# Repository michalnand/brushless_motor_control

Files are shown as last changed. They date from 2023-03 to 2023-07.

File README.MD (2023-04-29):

# stm32 FOC brushless motor controller

board

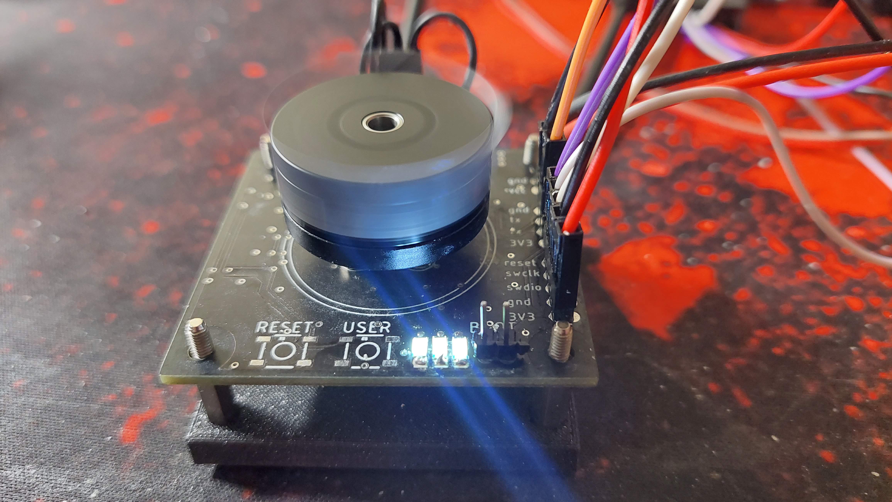
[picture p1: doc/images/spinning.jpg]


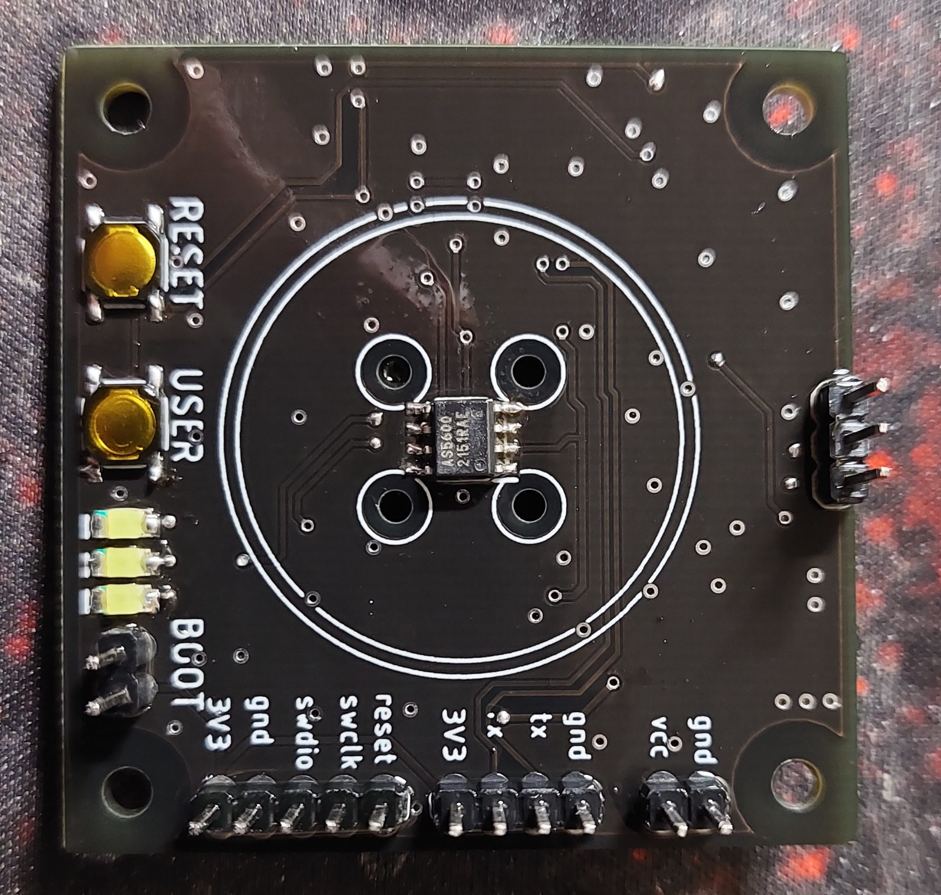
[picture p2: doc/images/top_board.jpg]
board

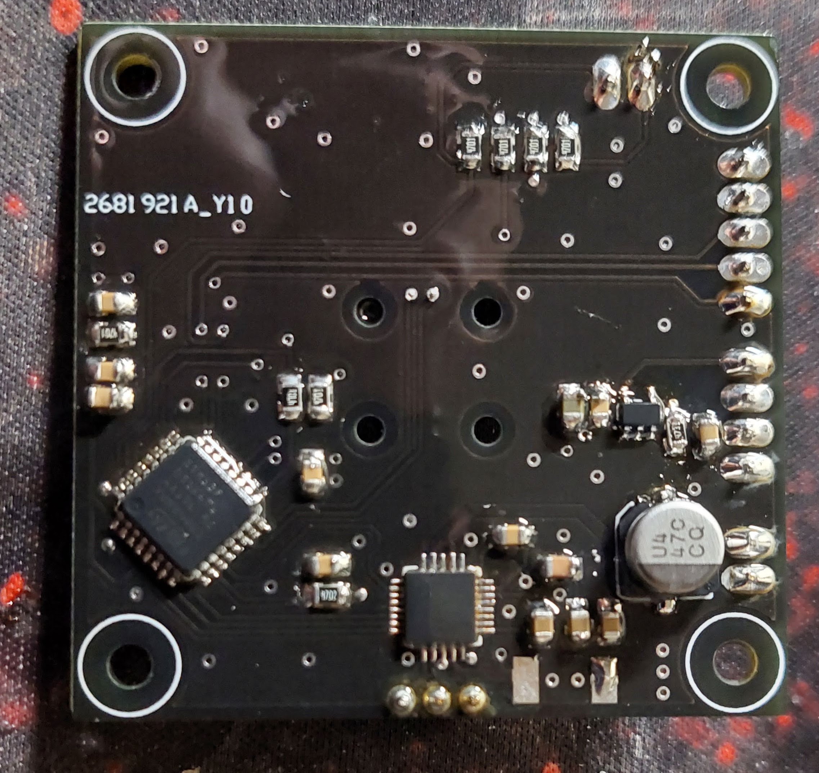
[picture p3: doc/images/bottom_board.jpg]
board


# repository

## utils : [utils](utils)
- testing utils and simulations
- transformation tests : transform_test.py
- PI current synthetis : pi_torque.ipynb
- LQR synthetis : lqr_design.ipynb
- requires [LibsControll](https://github.com/michalnand/libs_control)

## hardware : [hardware](hardware)
- eagle files
- 3D priting parts (jig for magnet centering)
- IMPORTANT - in schematic is wrong MP6540HA, correct is MP6540H (pwm only driver with enable)

- MCU   : stm32f051, arm cortex m0, 48MHz
- 3phase driver : MP6540H (DONT MP6540HA), 5A, 50V
- encoder : AS5600, 12bit, i2c

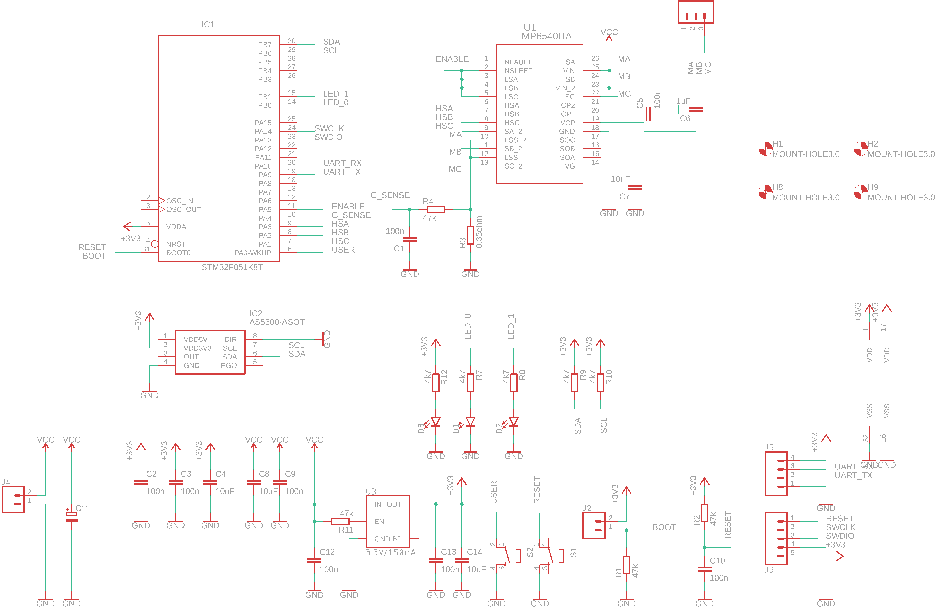
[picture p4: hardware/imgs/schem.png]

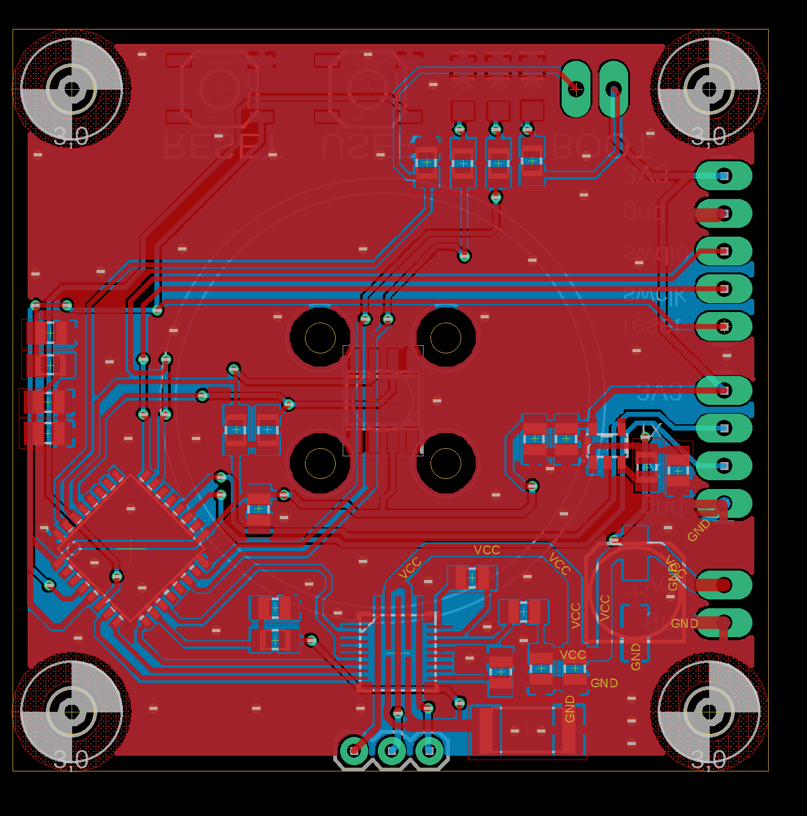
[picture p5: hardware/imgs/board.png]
board


## firmware : [firmware](firmware)
- main code for stm32f051
- core is in **user** folder
- see motor.cpp and motor_control.cpp to understand all details

# FOC block diagrams

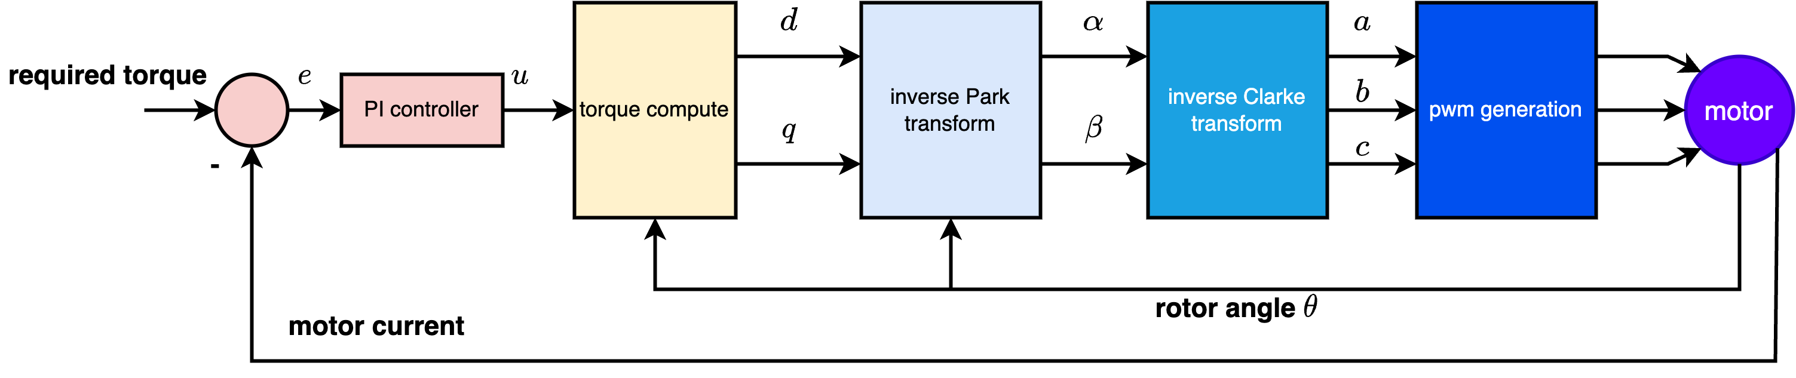
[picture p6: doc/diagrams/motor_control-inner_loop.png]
inner_loop


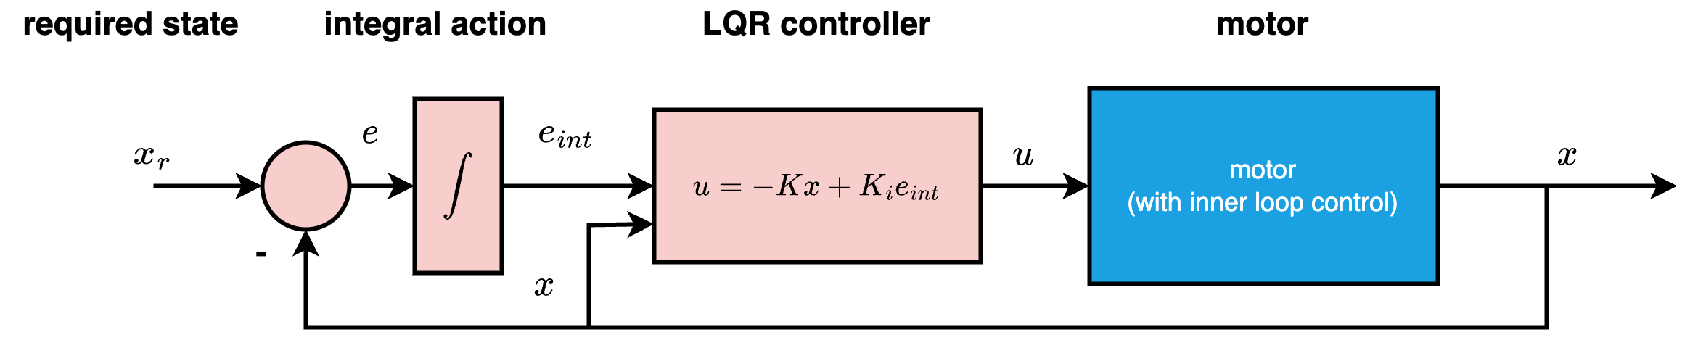
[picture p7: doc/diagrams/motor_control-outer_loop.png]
outer_loop


# transformation tests

basic tranformations tests :
- clarke - park - pwm scaling
- see [transform_test.py](utils/transform_test.py)

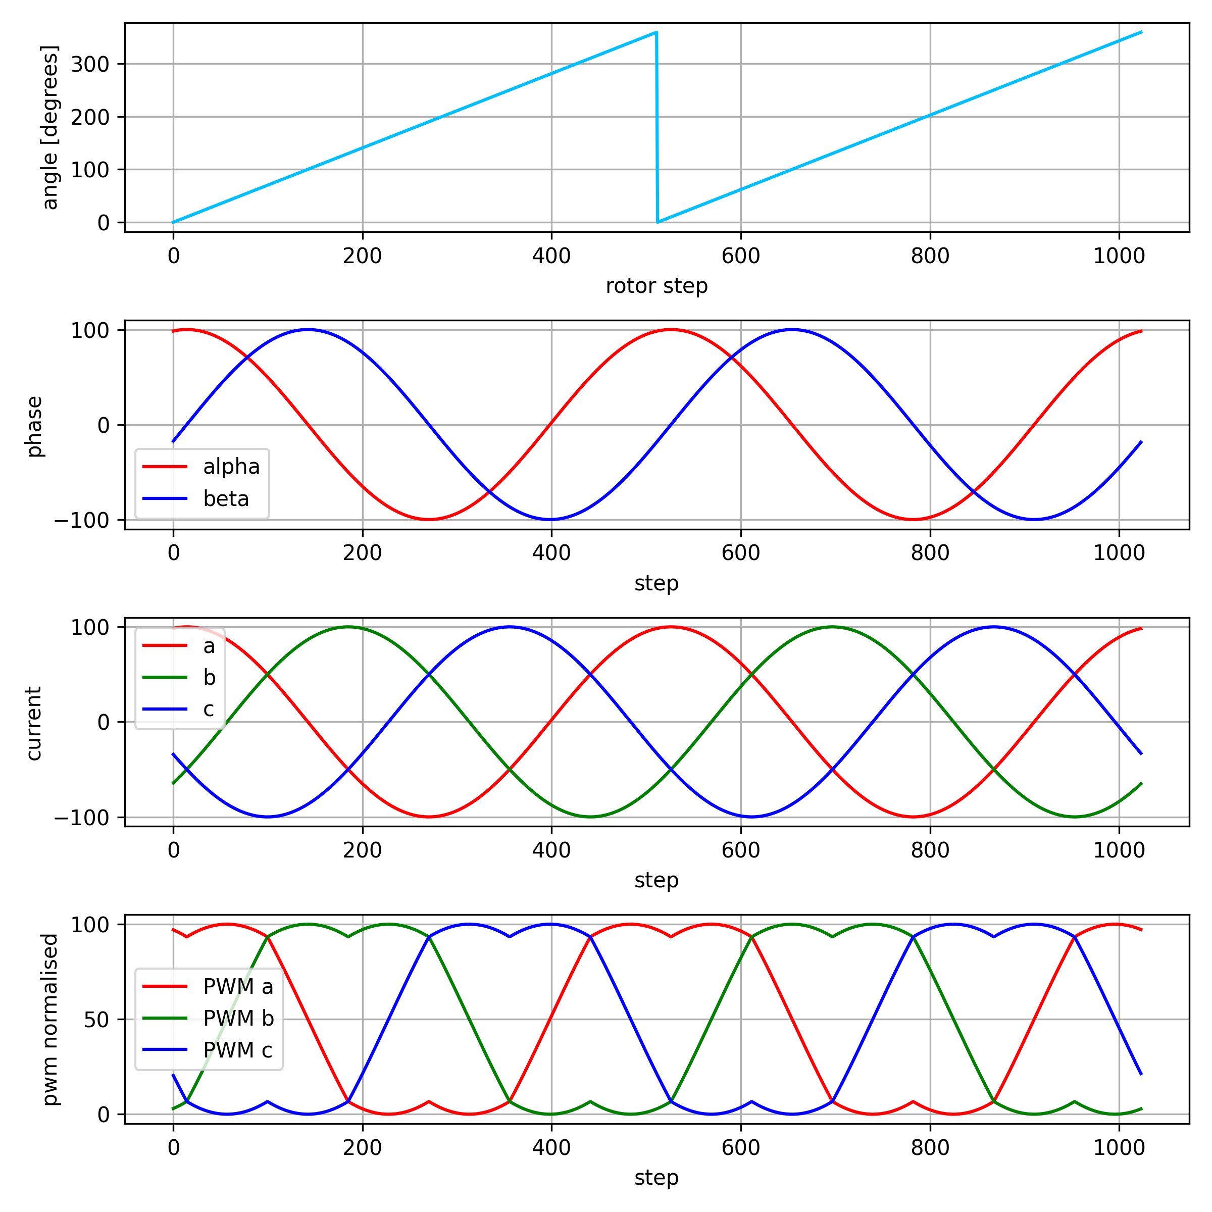
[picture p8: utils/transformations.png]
transformations


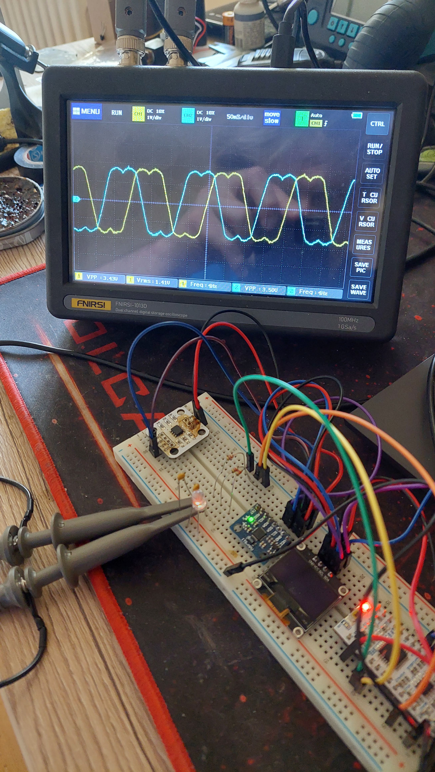
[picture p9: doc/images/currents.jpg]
currents


# fast running transformations in fixed point

## key features

- sine and cosine is precomputed, 1024 values arrays
- angle 2pi == 1024 (or 0) into tables
- theta ranges from <0, 1023>
- SINE_TABLE_MAX  represents "one", 1023 in tables
- square root of 3 is also precomputed, as fraction of x/1024 
- all divisions are by power of 2 - to avoid slow division
- this can easily run few kHz on cortex m0 (48MHz ARM)

```c++

#define SQRT3       ((int32_t)1773)      // sqrt(3)     = 1773/1024
#define SQRT3INV    ((int32_t)591)       // 1/sqrt(3)   = 591/1024

void Motor::set_park(int32_t d, int32_t q, uint32_t theta)
{
    //inverse Park transform
    int32_t alpha = (d*cos_tab(theta) - q*sin_tab(theta))/SINE_TABLE_MAX;
    int32_t beta  = (d*sin_tab(theta) + q*cos_tab(theta))/SINE_TABLE_MAX;

    this->set_clarke(alpha, beta);
}

void Motor::set_clarke(int32_t alpha, int32_t beta)
{
    //inverse Clarke transform
    int32_t a = alpha;
    int32_t b = -(alpha/2) + (SQRT3*beta)/(2*1024);
    int32_t c = -(alpha/2) - (SQRT3*beta)/(2*1024);

    this->set_phases(a, b, c); 
}

void Motor::set_phases(int32_t a, int32_t b, int32_t c)
{
    //transform into space-vector modulation, to achieve full voltage range
    int32_t min_val = min3(a, b, c);
    int32_t max_val = max3(a, b, c); 

    int32_t com_val = (min_val + max_val)/2;  

    //normalise into 0..MOTOR_CONTROL_MAX
    int32_t a_pwm = ((a - com_val)*SQRT3INV)/1024 + MOTOR_CONTROL_MAX/2;
    int32_t b_pwm = ((b - com_val)*SQRT3INV)/1024 + MOTOR_CONTROL_MAX/2;
    int32_t c_pwm = ((c - com_val)*SQRT3INV)/1024 + MOTOR_CONTROL_MAX/2;

    a_pwm = clamp((a_pwm*PWM_PERIOD)/MOTOR_CONTROL_MAX, 0, PWM_PERIOD);
    b_pwm = clamp((b_pwm*PWM_PERIOD)/MOTOR_CONTROL_MAX, 0, PWM_PERIOD);
    c_pwm = clamp((c_pwm*PWM_PERIOD)/MOTOR_CONTROL_MAX, 0, PWM_PERIOD);

    set_pwm(a_pwm, b_pwm, c_pwm);
}
```

# fast running PID in fixed point

- controller is first discretised in constructor 
- dt is sampling period in miliseconds
- kp, ki, kd are common controller constants, multiplied by 16384, to avoid floating point

```c++
k0 = kp + ((ki*dt)/1000) + ((kd*1000)/dt);
k1 = -kp - 2*((kd*1000)/dt);
k2 = ((kd*1000)/dt); 
```

- whole PID is just 3 multiplications and 4 additions
- to avoid integral windup, only clamping output is necessary 

```c++
int32_t PID::step(int32_t error)
{
    this->e2 = this->e1;
    this->e1 = this->e0;
    this->e0 = error;

    int32_t du = (k0*e0 + k1*e1 + k2*e2)/16384;
    u+= du;

    //anti windup
    if (u > antiwindup_max)
    {
        u = antiwindup_max;
    }
    
    if (u < antiwindup_min)
    {
        u = antiwindup_min;
    }

    return u;
}
```

# LQR position controller

see [lqr_design.ipynb](utils/lqr_design.ipynb)

## whole controller structure

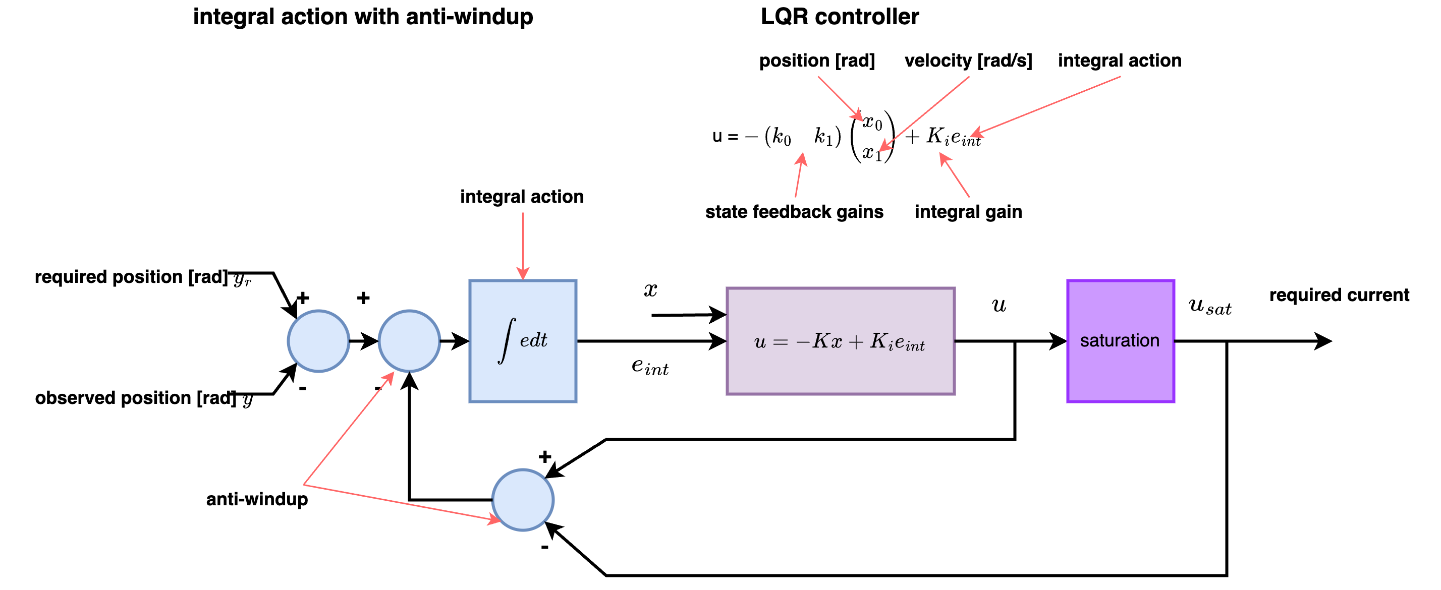
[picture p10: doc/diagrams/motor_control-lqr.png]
lqr_structure


## closed loop response + disturbance rejection

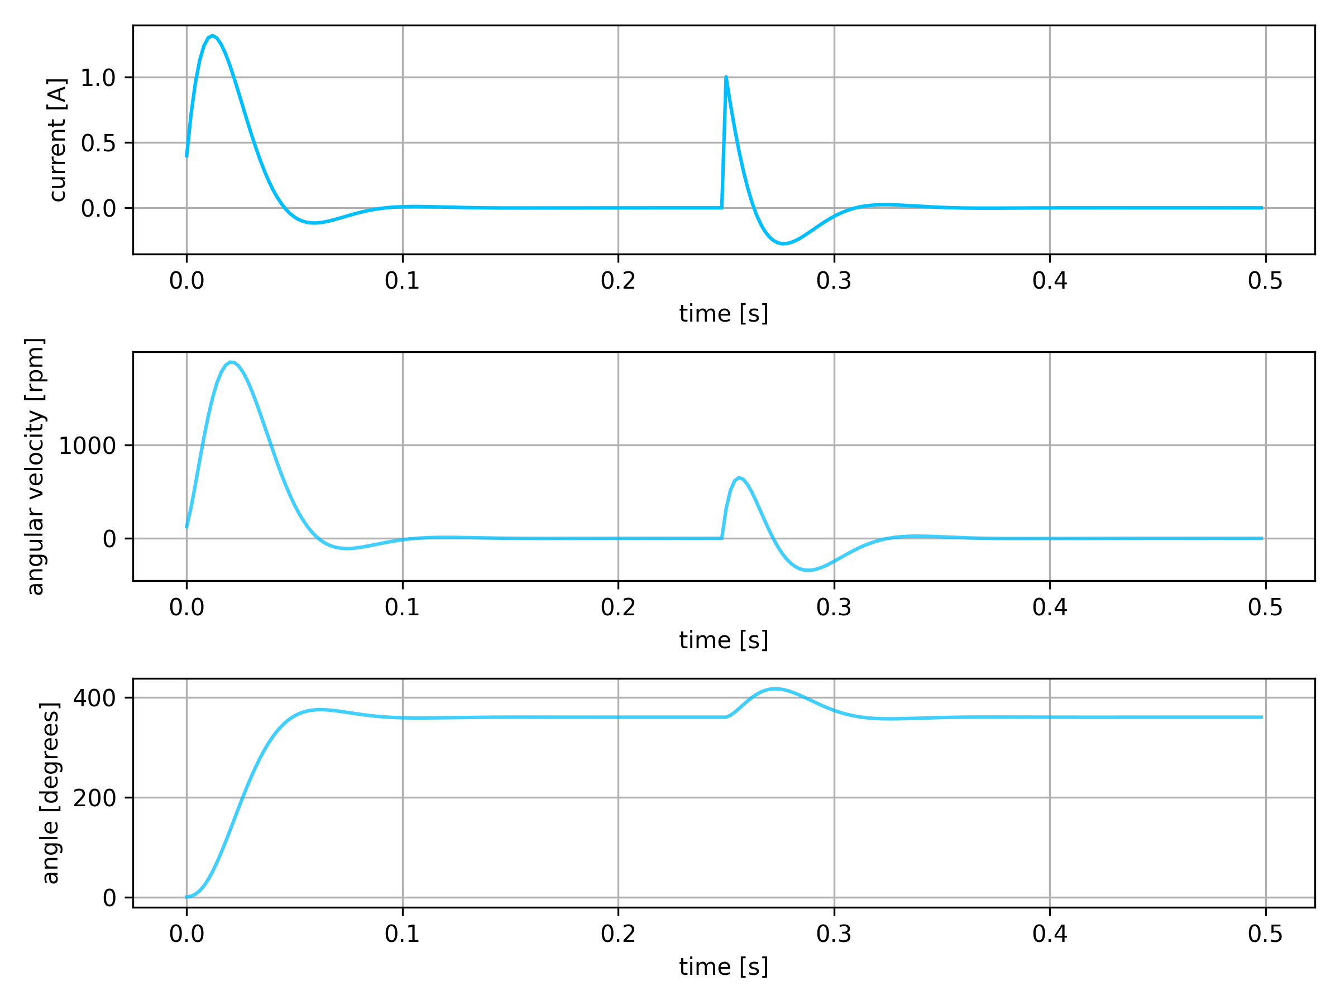
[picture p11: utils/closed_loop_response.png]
closed_loop_response


## poles

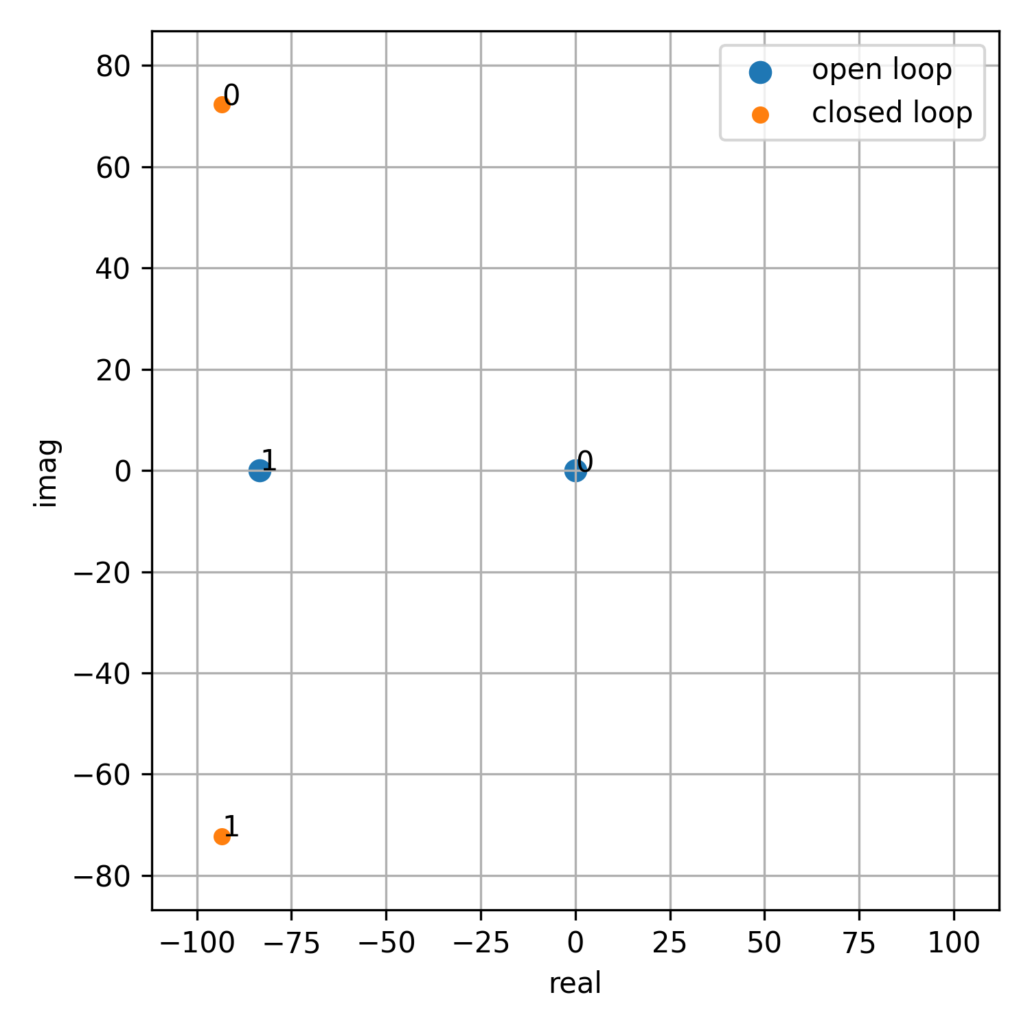
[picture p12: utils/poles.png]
poles


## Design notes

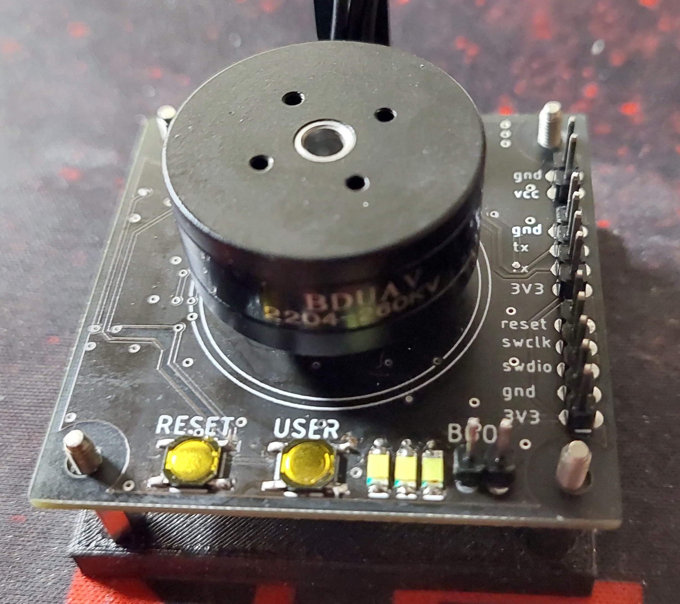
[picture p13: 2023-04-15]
doc/images/side_baord.jpg

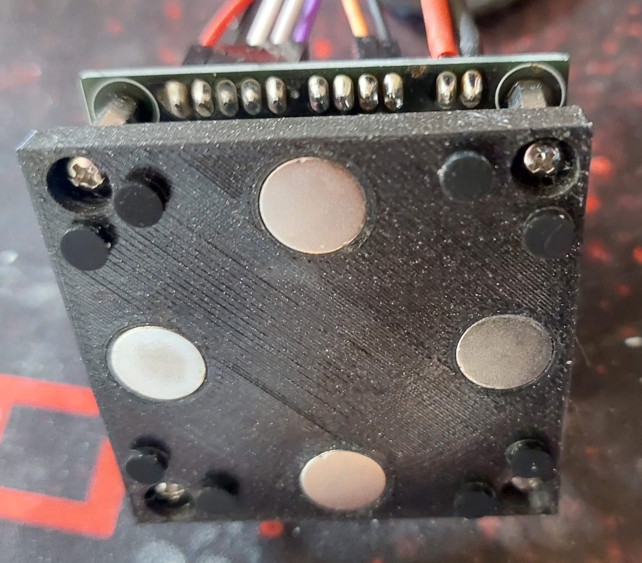
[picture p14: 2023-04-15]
doc/images/magnets.jpg

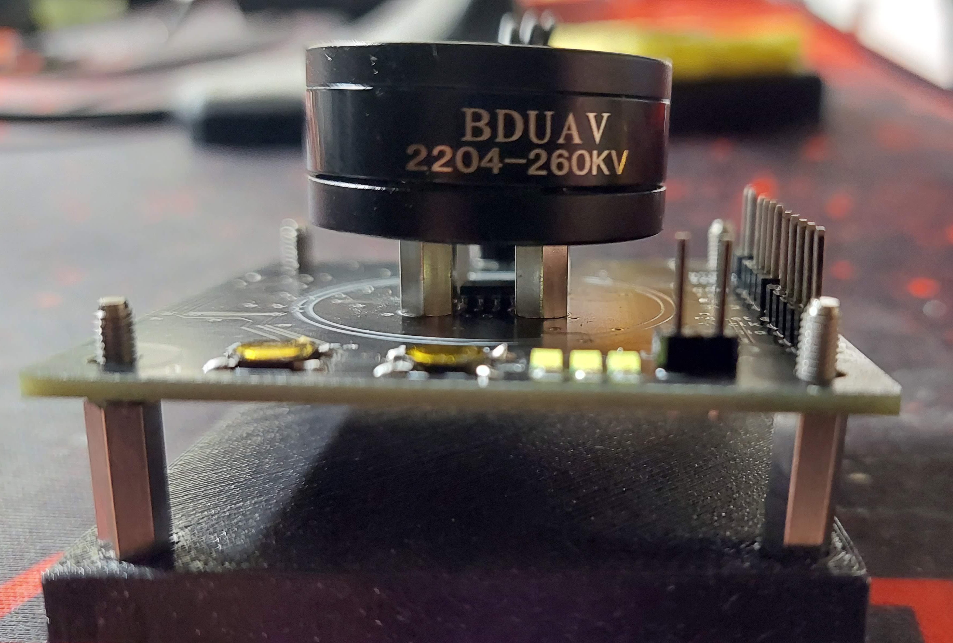
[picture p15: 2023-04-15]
doc/images/side_2_board.jpg

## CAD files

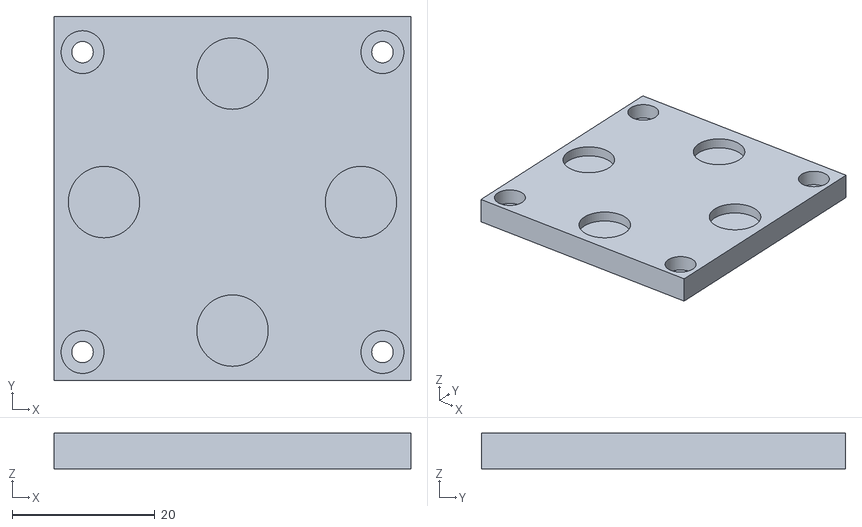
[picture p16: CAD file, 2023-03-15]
hardware/3d_print/motor_board_stand.stl
50.0 x 51.0 x 5.00

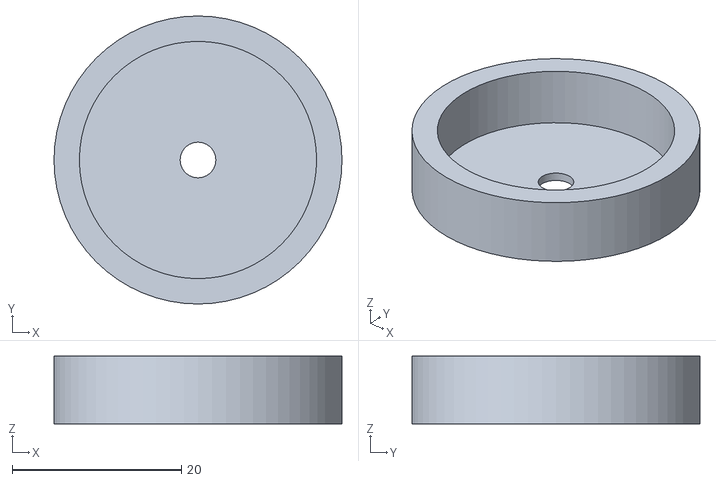
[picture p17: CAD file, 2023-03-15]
hardware/3d_print/magnet_center_jig.stl
34.0 x 34.0 x 8.00

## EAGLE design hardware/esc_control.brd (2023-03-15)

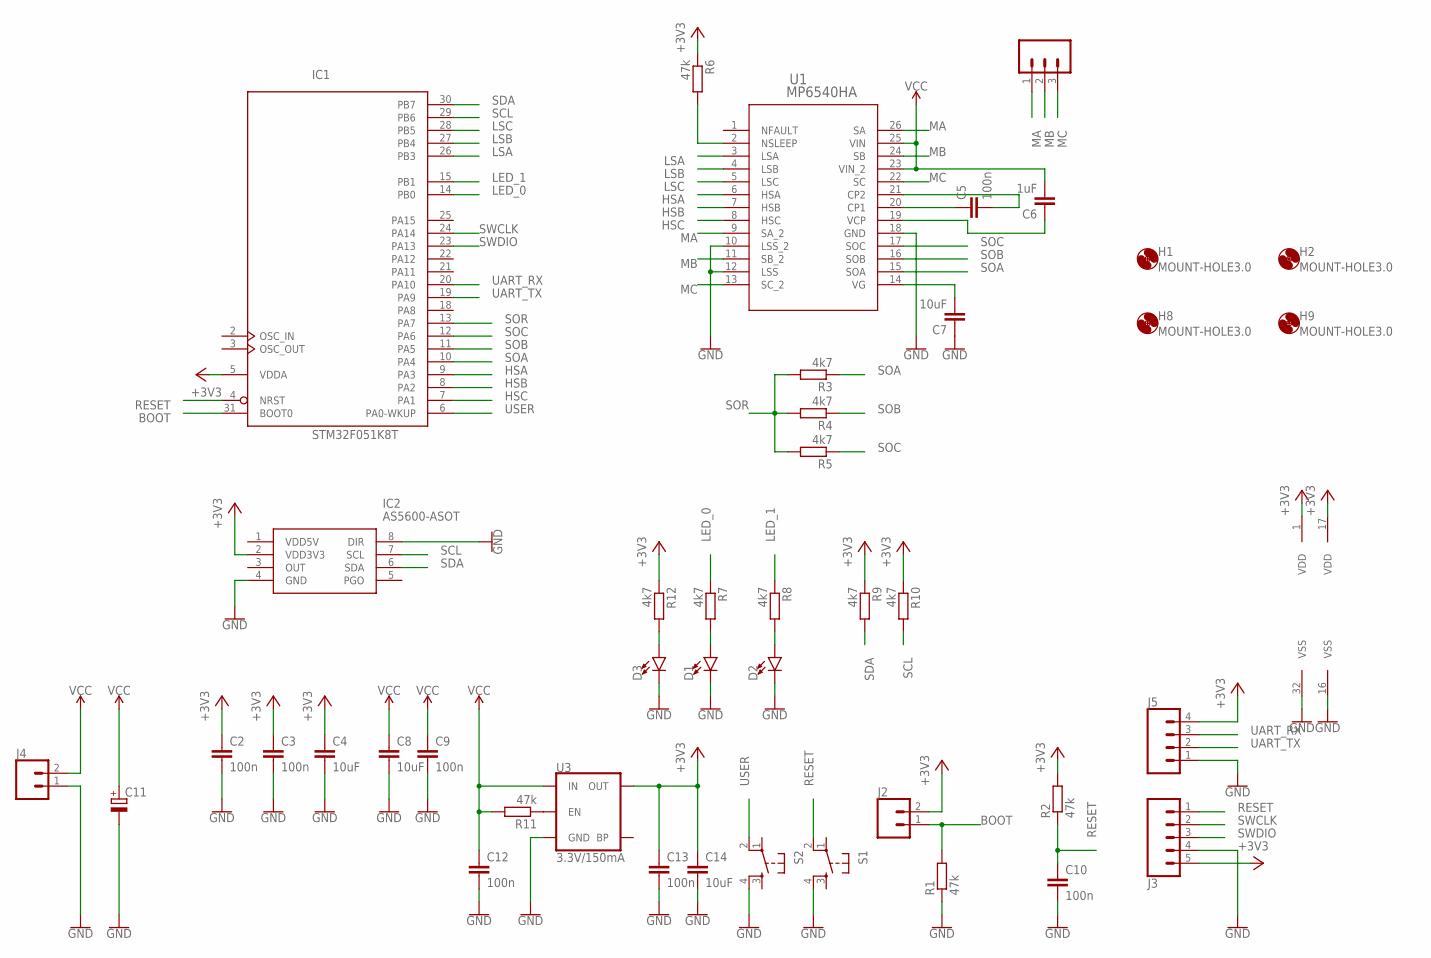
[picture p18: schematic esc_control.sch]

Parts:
C2, C3, C5, C9, C10, C12, C13: 100n; C0805
C4, C7, C8, C14: 10uF; C0805
C6: 1uF; C0805
C11: CPOL-EU153CLV-0605; 153CLV-0605
D1, D2, D3: LED1206; LED-1206
H1, H2, H8, H9: MOUNT-HOLE3.0; 3,0
IC1: STM32F051K8T; LQFP32
IC2: AS5600-ASOT; SOIC127P600X175-8N
J1: 455-1750-1-ND; 1X03
J2, J4: CONN_02PTH3; 1X02_LONGPADS
J3: CONN_05PTH_LONGPADS; 1X05_LONGPADS
J5: CONN_04LONGPADS; 1X04_LONGPADS
R1, R2, R6, R11: 47k; M0805
R3, R4, R5, R7, R8, R9, R10, R12: 4k7; M0805
S1, S2: TAC_SWITCHSMD; TACTILE-SWITCH-SMD
U1: MP6540HA; QFN-5X5_MP6540HA_MNP
U3: 3.3V/150mA; SOT23-5

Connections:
+3V3: C2.1, C3.1, C4.1, C13.1, C14.1, IC1.1 (VDD), IC1.5 (VDDA), IC1.17 (VDD), IC2.2 (VDD3V3), J2.2, J3.5, J5.4, R2.2, R6.1, R9.1, R10.1, R12.1, U3.5 (OUT)
BOOT: IC1.31 (BOOT0), J2.1, R1.2
GND: C2.2, C3.2, C4.2, C7.1, C8.2, C9.2, C10.2, C11.-, C12.2, C13.2, C14.2, D1.C, D2.C, D3.C, IC1.16 (VSS), IC1.32 (VSS), IC2.4 (GND), IC2.8 (DIR), J3.4, J4.1, J5.1, R1.1, S1.4, S2.4, U1.10 (LSS_2), U1.12 (LSS), U1.18 (GND), U3.2 (GND)
HSA: IC1.9 (PA3), U1.6 (HSA)
HSB: IC1.8 (PA2), U1.7 (HSB)
HSC: IC1.7 (PA1), U1.8 (HSC)
LED_0: IC1.14 (PB0), R7.1
LED_1: IC1.15 (PB1), R8.1
LSA: IC1.26 (PB3), U1.3 (LSA)
LSB: IC1.27 (PB4), U1.4 (LSB)
LSC: IC1.28 (PB5), U1.5 (LSC)
MA: J1.1, U1.9 (SA_2), U1.26 (SA)
MB: J1.2, U1.11 (SB_2), U1.24 (SB)
MC: J1.3, U1.13 (SC_2), U1.22 (SC)
unnamed: C5.1, U1.20 (CP1)
unnamed: C5.2, U1.21 (CP2)
unnamed: C6.1, U1.19 (VCP)
unnamed: R6.2, U1.2 (NSLEEP)
unnamed: C7.2, U1.14 (VG)
unnamed: D1.A, R7.2
unnamed: D2.A, R8.2
unnamed: R11.1, U3.3 (EN)
unnamed: D3.A, R12.2
RESET: C10.1, IC1.4 (NRST), J3.1, R2.1, S1.2
SCL: IC1.29 (PB6), IC2.7 (SCL), R10.2
SDA: IC1.30 (PB7), IC2.6 (SDA), R9.2
SOA: IC1.10 (PA4), R3.1, U1.15 (SOA)
SOB: IC1.11 (PA5), R4.1, U1.16 (SOB)
SOC: IC1.12 (PA6), R5.1, U1.17 (SOC)
SOR: IC1.13 (PA7), R3.2, R4.2, R5.2
SWCLK: IC1.24 (PA14), J3.2
SWDIO: IC1.23 (PA13), J3.3
UART_RX: IC1.20 (PA10), J5.3
UART_TX: IC1.19 (PA9), J5.2
USER: IC1.6 (PA0-WKUP), S2.2
VCC: C6.2, C8.1, C9.1, C11.+, C12.1, J4.2, R11.2, U1.23 (VIN_2), U1.25 (VIN), U3.1 (IN)

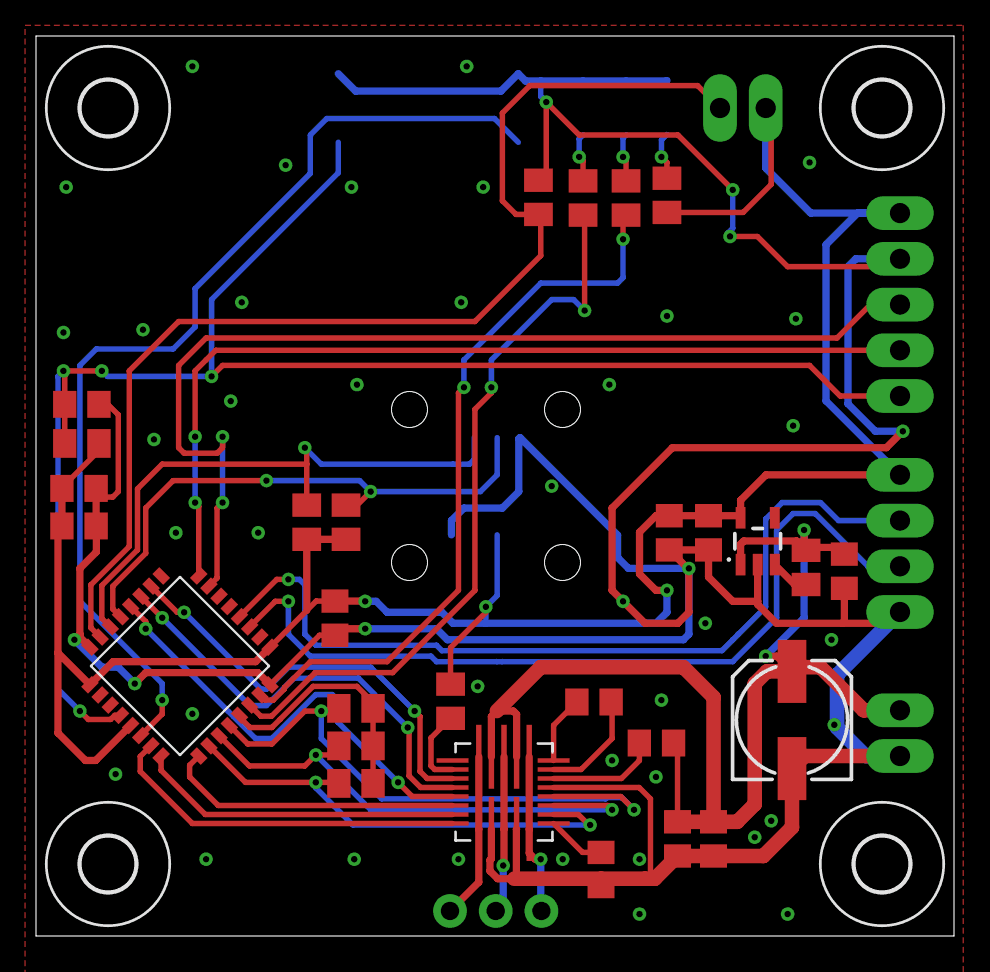
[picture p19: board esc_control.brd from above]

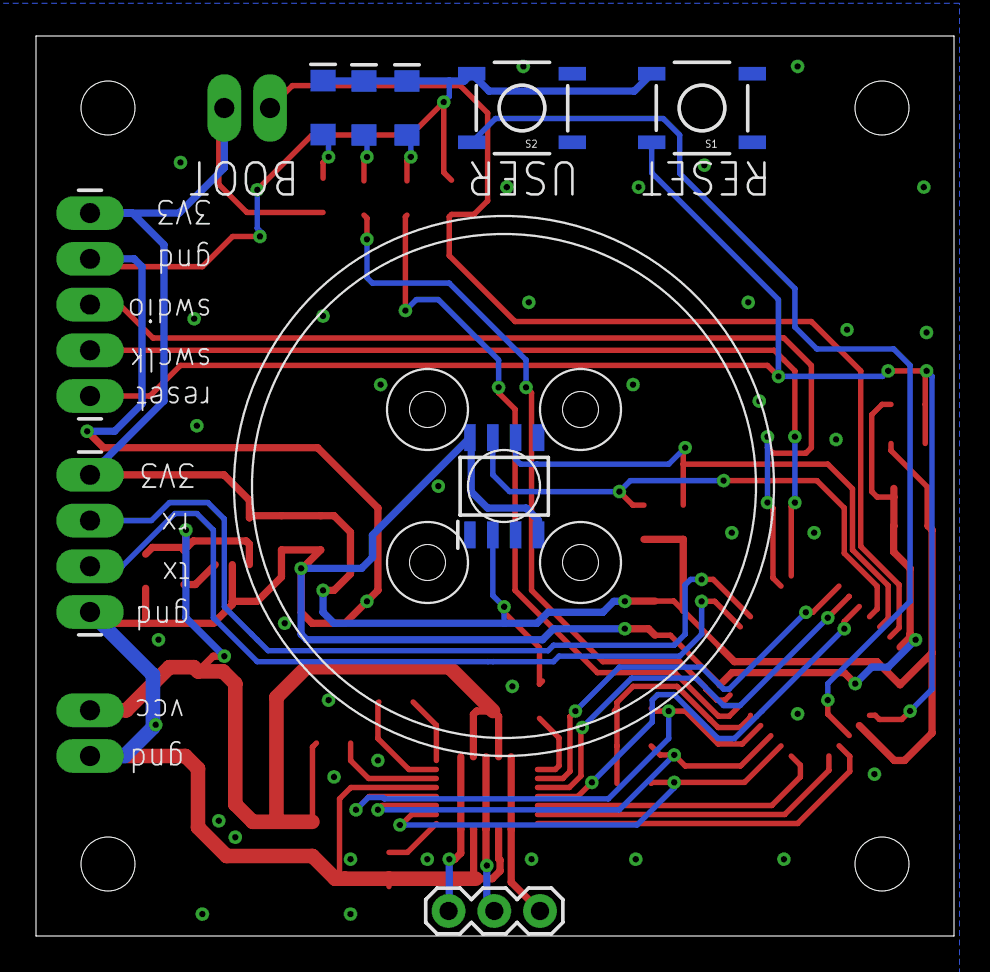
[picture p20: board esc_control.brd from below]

Board: 2 copper layers, 51.0 x 50.0 mm, 44 parts (12 on the bottom side), 36 nets.

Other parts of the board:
U$1: BRUSHLESS_GIMBAL_MOTOR_2204

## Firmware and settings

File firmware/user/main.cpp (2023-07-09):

#include "device.h"
#include <gpio.h>

#include <adc.h>
#include <i2c.h>
#include <as5600.h>
#include <motor.h>
#include <motor_control.h>

#include <gonio.h>

#include <test.h>
#include <terminal.h>
 
void SetPLL()
{
  RCC_PLLConfig(RCC_PLLSource_HSI, RCC_PLLMul_12);
  RCC_PLLCmd(ENABLE); 

  // Wait for PLLRDY after enabling PLL.
  while (RCC_GetFlagStatus(RCC_FLAG_PLLRDY) != SET)
  { 
    __asm("nop");
  } 

  // Select the PLL as clock source.
  RCC_SYSCLKConfig(RCC_SYSCLKSource_PLLCLK);  
  SystemCoreClockUpdate();
}


void delay_loops(uint32_t loops)
{
  while (loops--)
  {
    __asm("nop");
  }
}



MotorControl *g_motor_control;
volatile uint32_t g_ms_time = 0;

#ifdef __cplusplus
extern "C" {
#endif

void TIM16_IRQHandler(void)
{ 
  g_motor_control->callback_torque();
  g_ms_time++;
  TIM_ClearITPendingBit(TIM16, TIM_IT_CC1);  
}
 
void TIM17_IRQHandler(void)
{
    g_motor_control->callback(); 

    TIM_ClearITPendingBit(TIM17, TIM_IT_CC1);  
}
 
#ifdef __cplusplus
}
#endif
 
 
void timers_init()
{  
    TIM_TimeBaseInitTypeDef     TIM_TimeBaseStructure;
    NVIC_InitTypeDef            NVIC_InitStructure;

    //set timer 16 for 1kHz, and highest priority
    RCC_APB2PeriphClockCmd(RCC_APB2Periph_TIM16, ENABLE);

    TIM_TimeBaseStructure.TIM_Prescaler         = 0;
    TIM_TimeBaseStructure.TIM_CounterMode       = TIM_CounterMode_Up;
    TIM_TimeBaseStructure.TIM_Period            = 24000 - 1; //1kHz, 24MHz clock / 1000 - 1
    TIM_TimeBaseStructure.TIM_ClockDivision     = 0; 
    TIM_TimeBaseStructure.TIM_RepetitionCounter = 0;   

    TIM_TimeBaseInit(TIM16, &TIM_TimeBaseStructure);
    TIM_ITConfig(TIM16, TIM_IT_CC1, ENABLE);
    TIM_Cmd(TIM16, ENABLE); 

    NVIC_InitStructure.NVIC_IRQChannel = TIM16_IRQn;
    NVIC_InitStructure.NVIC_IRQChannelPriority = 0;
    NVIC_InitStructure.NVIC_IRQChannelCmd = ENABLE;
    NVIC_Init(&NVIC_InitStructure);


    //set timer 17 for 500Hz, and lower priority
    RCC_APB2PeriphClockCmd(RCC_APB2Periph_TIM17, ENABLE);

    TIM_TimeBaseStructure.TIM_Prescaler         = 0;
    TIM_TimeBaseStructure.TIM_CounterMode       = TIM_CounterMode_Up;

    TIM_TimeBaseStructure.TIM_Period            = 48000 - 1; //500Hz, 24MHz clock / 500 - 1
    TIM_TimeBaseStructure.TIM_ClockDivision     = 0;
    TIM_TimeBaseStructure.TIM_RepetitionCounter = 0;

    TIM_TimeBaseInit(TIM17, &TIM_TimeBaseStructure);
    TIM_ITConfig(TIM17, TIM_IT_CC1, ENABLE);
    TIM_Cmd(TIM17, ENABLE); 

    NVIC_InitStructure.NVIC_IRQChannel = TIM17_IRQn;
    NVIC_InitStructure.NVIC_IRQChannelPriority = 1;
    NVIC_InitStructure.NVIC_IRQChannelCmd = ENABLE;
    NVIC_Init(&NVIC_InitStructure);
}



void motor_identification(Terminal &terminal, MotorControl &motor_control)
{
  motor_control.required_current = MOTOR_CONTROL_MAX; 
  delay_loops(4000000);

  int32_t motor_max_current = 0;
  int32_t motor_max_speed   = 0;

  for (unsigned int i = 0; i < 1000; i++)
  {
    motor_max_current+= motor_control.motor_current;
    motor_max_speed+=   motor_control.angular_velocity;
    delay_loops(1000);
  } 

  motor_max_current = motor_max_current/1000;
  motor_max_speed   = motor_max_speed/1000;


  motor_control.required_current  = 0;
  delay_loops(500000);


  int32_t motor_max_speed_rpm = (motor_max_speed*60)/4096;
  
  terminal << "motor_max_current " << motor_max_current << " mA\n";
  terminal << "motor_max_speed   " << motor_max_speed_rpm   << " rpm\n";
  terminal << "angle             " << motor_control.angle_position   << "\n";

  int32_t time_start = g_ms_time;
  motor_control.required_current = MOTOR_CONTROL_MAX; 

  while (motor_control.angular_velocity < 0.632*motor_max_speed)
  {
    __asm("nop");
  }

  int32_t time_stop = g_ms_time;

  motor_control.required_current  = 0;
  delay_loops(500000);

  int32_t dt = time_stop - time_start; 

  terminal << "time_constant   " << dt   << " ms\n";
  terminal << "\n\n";
}

//const int32_t  required[] = {0, 1024, 0, -1024, 0, 2048, 0, -2048, 0, 4096, 0, -4096, 0, 4*4096, 0, -4*4096};

const int32_t  required[] = {0, 1024, 0, -1024, 0, 2048, 0, -2048, 0, 4096, 0, -4096, 0, 2*4096, 0, -2*4096};

 
int main(void)
{
    //cpu clock init
    SystemInit();

    // setup PLL, 6*HSI = 48MHz
    SetPLL();  
  
    Gpio<TGPIOB, 0, GPIO_MODE_OUT> led_0;
    Gpio<TGPIOB, 1, GPIO_MODE_OUT> led_1;
    Gpio<TGPIOA, 0, GPIO_MODE_IN_PULLUP> key_0;

    led_0 = 1;

    
    Terminal terminal;
    terminal.init(115200, USART1);
    terminal << "terminal init done\n";

    //encoder_test(terminal);

    
    MotorControl motor_control;
    motor_control.init();

    g_motor_control = &motor_control;
 
    timers_init();
    __enable_irq();

    //motor_identification( terminal, motor_control);

  
    g_ms_time = 0;

    unsigned int state = 0;
    
    float required_position = 0.0;
    while(1)
    {
      if ((g_ms_time%1000) < 50)
      { 
        led_0 = 1; 
      }
      else
      {
        led_0 = 0;
      }

    
      
      if ((g_ms_time%10) == 0)
      {
        if ((state == 0) && (key_0 == 0))
          state = 1;
        else if ((state == 1) && (key_0 == 1))
          state = 2;
        else if ((state == 2) && (key_0 == 0))
          state = 3;
        else if ((state == 3) && (key_0 == 1))
          state = 0;
      }
      
      if (state == 0)
      {
        led_1 = 0;

        motor_control.required_position = 0;
      }


      if (state == 2)
      {
        led_1 = 1; 
        
        uint32_t required_idx = (g_ms_time/1000)%16;
        motor_control.required_position = required[required_idx];

        
        //motor_control.required_position = motor_control.angle_position + 20.0;
        
      } 
      
      if ((g_ms_time%100) == 0)
      {
        int32_t angle_deg = (motor_control.angle_position*360)/4096;
        int32_t speed_rpm = (motor_control.angular_velocity*60)/4096;
        
        terminal << "current " << motor_control.motor_current << " mA\n";
        terminal << "angle " << angle_deg << " deg\n";
        terminal << "speed " << speed_rpm << " rpm\n";
        //terminal << "error_sum " << motor_control.error_sum << " deg\n";
        terminal << "\n\n";
      }
    }
    

  
  

    return 0;
} 

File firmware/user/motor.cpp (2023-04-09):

#include "motor.h"

#include <gonio.h>
#include <device.h>


//helping stuff
#define SQRT3       ((int32_t)1773)      // sqrt(3)     = 1773/1024
#define SQRT3INV    ((int32_t)591)       // 1/sqrt(3)   = 591/1024

#define max2(x,y) (((x) >= (y)) ? (x) : (y))
#define min2(x,y) (((x) <= (y)) ? (x) : (y))

#define max3(x, y, z) (max2(max2(x, y), z))
#define min3(x, y, z) (min2(min2(x, y), z))


Motor::Motor()
{
    
}

Motor::~Motor()
{

}

void Motor::init()
{
    this->hw_init();
}


void Motor::hold()
{
    this->set_torque(500, 0, 0);

    uint32_t loops = 4000000;
    while (loops--) 
    {
        __asm("nop"); 
    } 
}
    

void Motor::release()
{
    this->set_torque(0, 0, 0);

    uint32_t loops = 4000000;
    while (loops--) 
    {
        __asm("nop"); 
    } 
}
    


void Motor::set_torque(int32_t torque, uint32_t phase, uint32_t rotor_angle)
{
    int32_t q = (torque*cos_tab(phase))/SINE_TABLE_MAX;
    int32_t d = (torque*sin_tab(phase))/SINE_TABLE_MAX;

    this->set_park(d, q, (rotor_angle*MOTOR_POLES)/(2*4));
}

 
void Motor::set_park(int32_t d, int32_t q, uint32_t theta)
{
    //inverse Park transform
    int32_t alpha = (d*cos_tab(theta) - q*sin_tab(theta))/SINE_TABLE_MAX;
    int32_t beta  = (d*sin_tab(theta) + q*cos_tab(theta))/SINE_TABLE_MAX;

    this->set_clarke(alpha, beta);
}

void Motor::set_clarke(int32_t alpha, int32_t beta)
{
    //inverse Clarke transform
    int32_t a = alpha;
    int32_t b = -(alpha/2) + (SQRT3*beta)/(2*1024);
    int32_t c = -(alpha/2) - (SQRT3*beta)/(2*1024);


    this->set_phases(a, b, c); 
}

void Motor::set_phases(int32_t a, int32_t b, int32_t c)
{
    //transform into space-vector modulation, to achieve full voltage range
    int32_t min_val = min3(a, b, c);
    int32_t max_val = max3(a, b, c); 

    int32_t com_val = (min_val + max_val)/2;  

    //normalise into 0..MOTOR_CONTROL_MAX
    int32_t a_pwm = ((a - com_val)*SQRT3INV)/1024 + MOTOR_CONTROL_MAX/2;
    int32_t b_pwm = ((b - com_val)*SQRT3INV)/1024 + MOTOR_CONTROL_MAX/2;
    int32_t c_pwm = ((c - com_val)*SQRT3INV)/1024 + MOTOR_CONTROL_MAX/2;
    
     
    a_pwm = clamp((a_pwm*PWM_PERIOD)/MOTOR_CONTROL_MAX, 0, PWM_PERIOD);
    b_pwm = clamp((b_pwm*PWM_PERIOD)/MOTOR_CONTROL_MAX, 0, PWM_PERIOD);
    c_pwm = clamp((c_pwm*PWM_PERIOD)/MOTOR_CONTROL_MAX, 0, PWM_PERIOD);

    set_pwm(a_pwm, b_pwm, c_pwm);
}



void Motor::hw_init()
{
    GPIO_InitTypeDef GPIO_InitStruct;
    
    //PWM controll pins 
    //PWMA : PA3, TIM2_CH4
    //PWMB : PA2, TIM2_CH3
    //PWMC : PA1, TIM2_CH2

    //RCC_APB1PeriphClockCmd(RCC_AHBPeriph_GPIOA, ENABLE);

    RCC->AHBENR|= RCC_AHBENR_GPIOAEN;
 
    
    //init pins
    GPIO_InitStruct.GPIO_Pin    = GPIO_Pin_1 | GPIO_Pin_2 | GPIO_Pin_3;
    GPIO_InitStruct.GPIO_OType  = GPIO_OType_PP;
    GPIO_InitStruct.GPIO_PuPd   = GPIO_PuPd_NOPULL;
    GPIO_InitStruct.GPIO_Mode   = GPIO_Mode_AF;
    GPIO_InitStruct.GPIO_Speed  = GPIO_Speed_10MHz;
    GPIO_Init(GPIOA, &GPIO_InitStruct);

    //alternating functions for pins
    GPIO_PinAFConfig(GPIOA, GPIO_PinSource3, GPIO_AF_2);
    GPIO_PinAFConfig(GPIOA, GPIO_PinSource2, GPIO_AF_2);
    GPIO_PinAFConfig(GPIOA, GPIO_PinSource1, GPIO_AF_2);
    


    //enable controll pin, PA5
    RCC->AHBENR|= RCC_AHBENR_GPIOAEN;
    
    //init pins
    GPIO_InitStruct.GPIO_Pin    = GPIO_Pin_5;
    GPIO_InitStruct.GPIO_OType  = GPIO_OType_PP;
    GPIO_InitStruct.GPIO_PuPd   = GPIO_PuPd_NOPULL;
    GPIO_InitStruct.GPIO_Mode   = GPIO_Mode_OUT;
    GPIO_InitStruct.GPIO_Speed  = GPIO_Speed_Level_1;
    GPIO_Init(GPIOA, &GPIO_InitStruct);

    


    //init timer 2

    TIM_TimeBaseInitTypeDef TIM_BaseStruct;

    //enable clock for timer 2
    RCC_APB1PeriphClockCmd(RCC_APB1Periph_TIM2, ENABLE);
    //RCC->AHBENR|= RCC_APB1ENR_TIM2EN;

    
    // PWM_frequency = timer_clk / (TIM_Period + 1)
    // TIM_Period = timer_clk / PWM_frequency - 1
    TIM_BaseStruct.TIM_Prescaler    = 0;
    TIM_BaseStruct.TIM_CounterMode  = TIM_CounterMode_Up;

    TIM_BaseStruct.TIM_Period               = PWM_PERIOD;
    TIM_BaseStruct.TIM_ClockDivision        = TIM_CKD_DIV1;
    TIM_BaseStruct.TIM_RepetitionCounter    = 0;
	 
    // Initialize TIM2
    TIM_TimeBaseInit(TIM2, &TIM_BaseStruct);
    TIM_Cmd(TIM2, ENABLE);

    //stop motor    
    this->set_pwm(0, 0, 0);

    //set enable to high, for all phases
    GPIOA->ODR |= (1<<5); 
}


void Motor::set_pwm(uint32_t a_pwm, uint32_t b_pwm, uint32_t c_pwm)
{
    //PWM output settings
    TIM_OCInitTypeDef TIM_OCStruct;
    
    // PWM mode 2 : clear on compare match
    // PWM mode 1 : set on compare match
    TIM_OCStruct.TIM_OCMode         = TIM_OCMode_PWM2;
    TIM_OCStruct.TIM_OutputState    = TIM_OutputState_Enable;
    TIM_OCStruct.TIM_OCPolarity     = TIM_OCPolarity_Low;

    //HSA pwm, PA3, TIM2_CH4
    TIM_OCStruct.TIM_Pulse = b_pwm;
    TIM_OC4Init(TIM2, &TIM_OCStruct);
    TIM_OC4PreloadConfig(TIM2, TIM_OCPreload_Enable);

    //HSB pwm, PA2, TIM2_CH3
    TIM_OCStruct.TIM_Pulse = a_pwm;
    TIM_OC3Init(TIM2, &TIM_OCStruct);
    TIM_OC3PreloadConfig(TIM2, TIM_OCPreload_Enable);

    //HSC pwm, PA1, TIM2_CH2
    TIM_OCStruct.TIM_Pulse = c_pwm;
    TIM_OC2Init(TIM2, &TIM_OCStruct);
    TIM_OC2PreloadConfig(TIM2, TIM_OCPreload_Enable);
}



int32_t Motor::clamp(int32_t value, int32_t min, int32_t max)
{
    if (value > max)
    {
        value = max;
    }

    if (value < min)
    {
        value = min;
    }

    return value;
}

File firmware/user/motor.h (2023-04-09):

#ifndef _MOTOR_H_
#define _MOTOR_H_

/*
    PWM controll pins :

    PWMA : PA3, TIM2_CH4
    PWMB : PA2, TIM2_CH3
    PWMC : PA1, TIM2_CH2


    enable controll pins:

    ENA : PB3, TIM2_CH2
    ENB : PB4, TIM3_CH1
    ENC : PB5, TIM3_CH2
*/

 


#define MOTOR_CONTROL_MAX       ((int32_t)1024)

#define MOTOR_POLES             ((int32_t)14)
#define MOTOR_KV                ((int32_t)250)
#define MOTOR_CURRENT_MAX       ((int32_t)5)


  
//20kHz PWM, 48MHz is timer 2 clock source
#define PWM_FREQUENCY           ((uint32_t)20000)
#define PWM_PERIOD              ((uint32_t)24000000/PWM_FREQUENCY - 1)

//maximal motor torque x 4096
#define MOTOR_TORQUE_MAX        ((4096*MOTOR_CURRENT_MAX)/MOTOR_KV)


#include <stdint.h>
#include <as5600.h>
#include <pid.h>

class Motor
{
    public:
        Motor();

        virtual ~Motor();

        void init();

        void hold();
        void release();


        /*
            main motor control

            torque t in range 0..MOTOR_CONTROL_MAX
            phase       : TODO, 0..SINE_TABLE_SIZE
            rotor_angle : measured rotor angle, 0..4096 (as from encoder)
        */
        void set_torque(int32_t torque, uint32_t phase, uint32_t rotor_angle);

        //inverse Park transform
        //can be used for PI torque control
        void set_park(int32_t d, int32_t q, uint32_t theta);


    public:
        //inverse Clarke transform
        void set_clarke(int32_t alpha, int32_t beta);

        //transform into space-vector modulation, to achieve full voltage range
        void set_phases(int32_t a, int32_t b, int32_t c);

    private:
        void    hw_init();
        void    set_pwm(uint32_t a_pwm, uint32_t b_pwm, uint32_t c_pwm);
        int32_t clamp(int32_t value, int32_t min, int32_t max);
};

#endif

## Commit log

2023-03-15 hardware done
    [esc_control.brd, esc_control.sch, magnet_center_jig.stl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]
2023-03-15 motor control basic
2023-03-19 pi controller
    [esc_control_2.brd, esc_control_2.sch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]
2023-05-21 filter for position

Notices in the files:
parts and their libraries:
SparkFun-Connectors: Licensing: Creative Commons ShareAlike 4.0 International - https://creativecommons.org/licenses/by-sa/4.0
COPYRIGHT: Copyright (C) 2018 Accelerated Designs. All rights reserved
